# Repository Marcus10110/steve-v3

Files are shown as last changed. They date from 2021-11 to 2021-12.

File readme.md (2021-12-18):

# Steve the Bartending Robot

PCB Revision 3

Steve the bartending robot is a robotic drink maker, capable of dispensing 24 different liquids for mixing cocktails.

## Hardware Guide

### Electronics
The Steve V3 PCB design files can be found in the BarBot3 directory.

The schematics and layout were created with [KiCad](https://www.kicad.org/)

The board can also be ordered directly from [OSHPARK](https://oshpark.com/) [here](https://oshpark.com/shared_projects/AuEMTmuf).

The bill of materials for the PCB, pumps, and wire harness for the pumps is available on [octopart](https://octopart.com/) [here](https://octopart.com/bom-tool/abOfMIaY).

The design also requires a 12V, 4A+ power supply with a 5.5x2.1mm barrel jack, and a USB-C cable, for USB 2.0 data.

The power supply current rating is the limiting factor for the number of pumps which can be turned on simultaneously.

The parts list include includes wire, connectors, and crimps for assembling the pump motor wire harnesses.

Additionally, a crimp tool is needed to crimp the connectors into the wire. **TODO: find PN and place here.**

We assembled the pumps all with the same wire length, long enough to reach from the PCB to the furthest pump with some spare distance.

The connector pin 1 should be connected to the positive side of the pump, and pin 2 should be connected to the negative side.

**TODO: add wire assembly detail here**

### Mechanical

To hold all the pumps and the PCB together. This was laser cut from acrylic. The CAD design can be found on [onshape](https://www.onshape.com/en/) [here](https://cad.onshape.com/documents/0a76c84c79ce9e6492f21b7e/w/e3ece1aa1a5ce6af157ea8d7/e/032fdd28f397ef2ffe8feb1f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).

In addition to the laser cut mount, the following parts are needed:
- [Wood Furniture Legs](https://www.amazon.com/gp/product/B07DF68BN7/ref=ppx_yo_dt_b_search_asin_image?ie=UTF8&psc=1)
- M2.5 thermal threaded inserts x48
- M3 thermal threaded inserts x3
- 3/4 inch wood screws #8 x4
- M2.5 screws x48
- M3 standoffs x3
- M3 screws x3

**TODO: add McMaster links**

### Firmware

The firmware is developed using the Arduino software, and can be found in the BarBot3Firmware folder.

The hardware implementation was based off of Sparkfun's [SparkFun Qwiic Pro Micro](https://www.sparkfun.com/products/15795), which is essentially a Sparkfun Pro Micro but with a USB-C connector.

In the arduino software, you will want to install the Sparkfun board library, and select the Sparkfun Pro Micro 3.3V / 8 MHz board. Install instructions can be found [here](https://github.com/sparkfun/Arduino_Boards#installation-instructions).

Also, install the "Adafruit MCP23008 Library" from the library manager.

It's important to mention that the microcontroller does not support USB bus power, so the 12V power supply must be connected in order for the microcontroller to run.

Before the firmware can be loaded onto the microcontroller, the Arduino bootloader needs to be loaded onto the ATMEGA32U4. This can be done in a number of ways, however the simplest is to use the AVR-ISP MK2.

**TODO: link to an actually good FW flashing article**

Once the Arduino bootloader has been flashed, the device should enumerate as a serial port over USB.

The BarBot3Firmware project should compile successfully once the required library is installed. Be sure the board mentioned above is selected. Then download the firmware.

To verify the design is working, open the serial monitor in the Arduino software, and type and send "DEBUG". This will print out a list of 24 zeros, indicating that all pumps are off. This command is for debugging only, and prints out the number of milliseconds each pump will remain on. Once a pump reaches zero, the pump will turn off.

Refer to the comments at the top of BarBat3Firmware.ino for documentation on the supported commands

**TODO: move firmware command documentation here**

### Software

**TODO: Link to SW repository here.**

## Operating Guide

**TODO: write operating guide here**

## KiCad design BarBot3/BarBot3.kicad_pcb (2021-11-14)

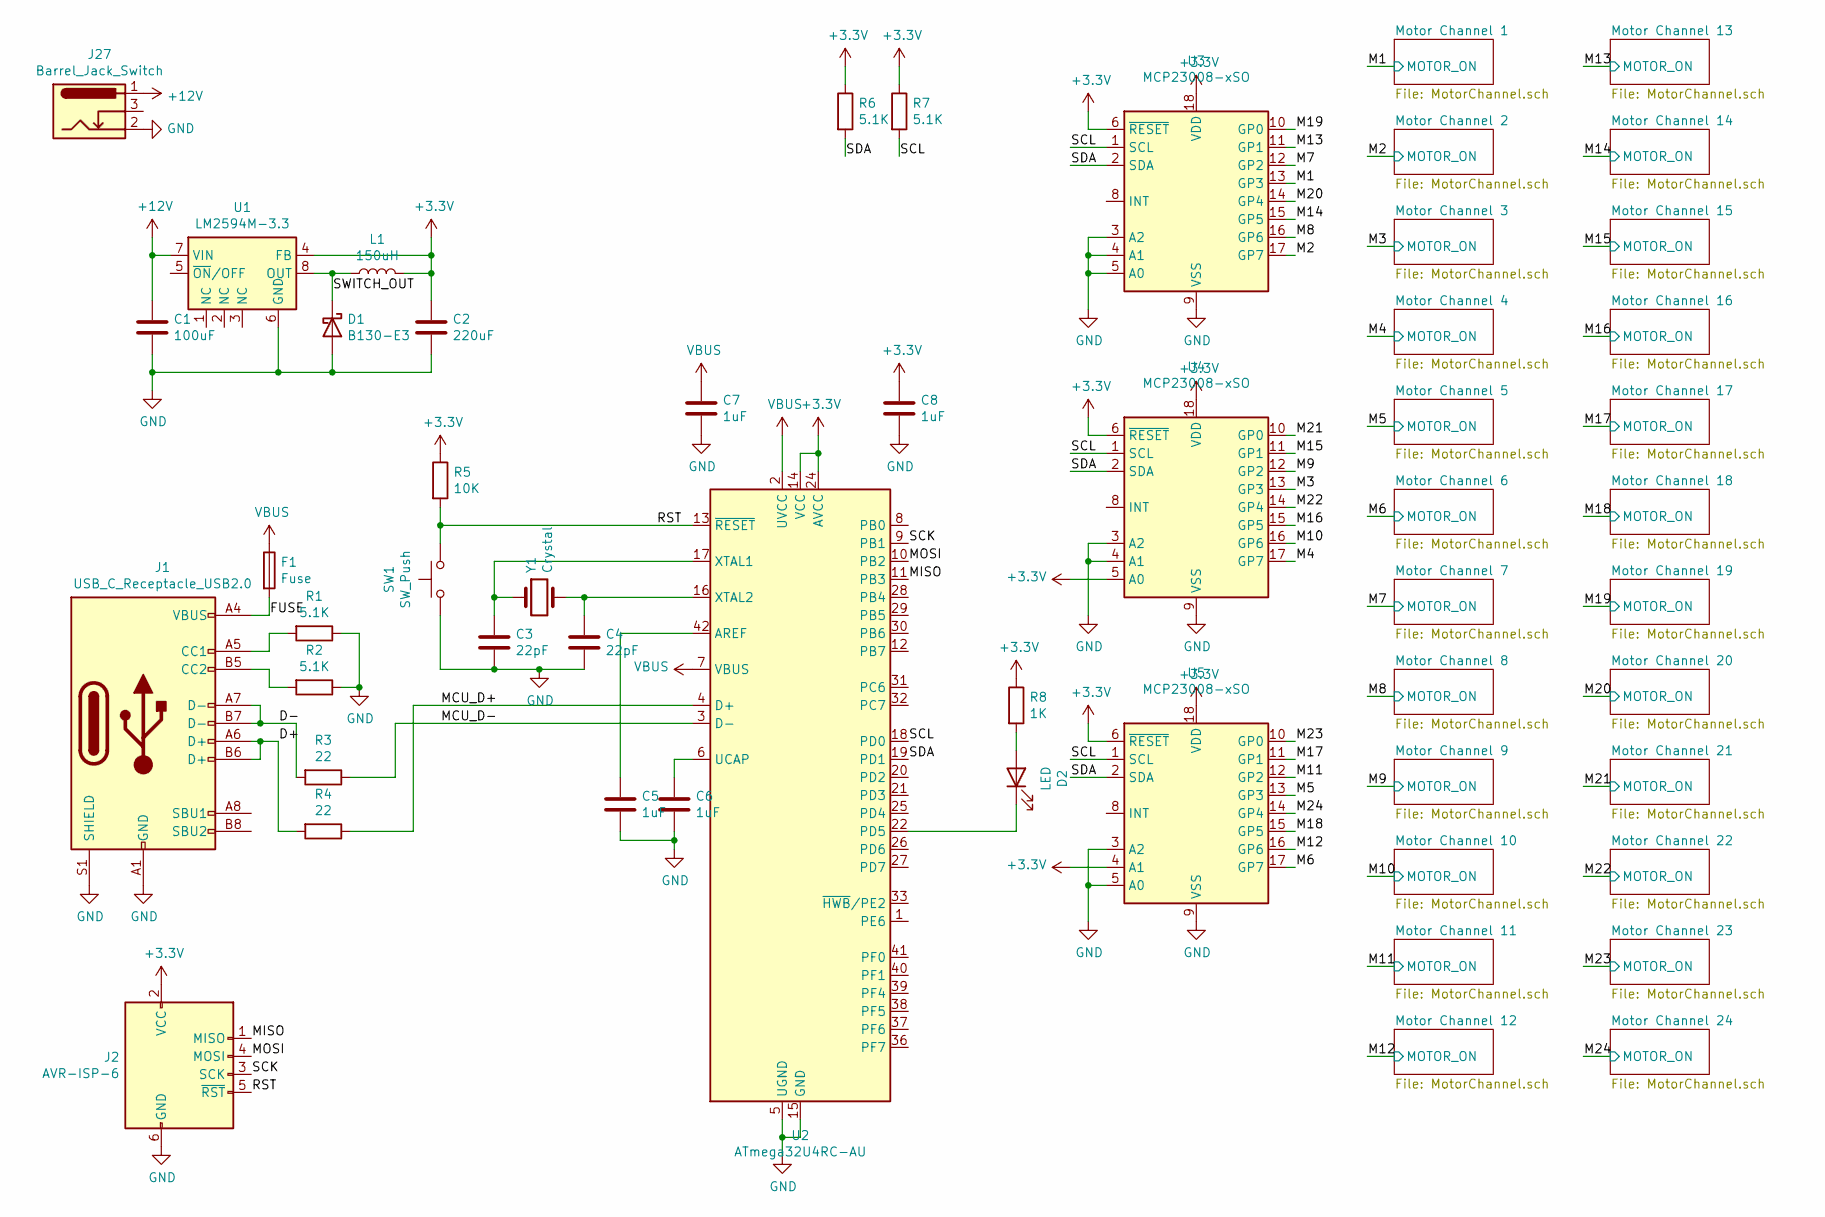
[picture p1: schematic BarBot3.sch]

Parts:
C1: 100uF; C_Elec_8x10.2
C2: 220uF; CP_Elec_10x10
C3, C4: 22pF; C_0805_2012Metric_Pad1.18x1.45mm_HandSolder
C5, C6, C7, C8: 1uF; C_0805_2012Metric_Pad1.18x1.45mm_HandSolder
D1: B130-E3; D_SOD-123
D2: LED; LED_PLCC-2
F1: Fuse; Fuse_1206_3216Metric_Pad1.42x1.75mm_HandSolder
J1: USB_C_Receptacle_USB2.0; USB_C_Receptacle_GCT_USB4085
J2: AVR-ISP-6; PinHeader_2x03_P2.54mm_Vertical
J27: Barrel_Jack_Switch; BarrelJack_CUI_PJ-102AH_Horizontal
L1: 150uH; L_Bourns_SRR1210A
R1, R2, R6, R7: 5.1K; R_0805_2012Metric_Pad1.20x1.40mm_HandSolder
R3, R4: 22; R_0805_2012Metric_Pad1.20x1.40mm_HandSolder
R5: 10K; R_0805_2012Metric_Pad1.20x1.40mm_HandSolder
R8: 1K; R_0805_2012Metric_Pad1.20x1.40mm_HandSolder
SW1: SW_Push; SW_Push_1P1T_NO_6x6mm_H9.5mm
U1: LM2594M-3.3; SOIC-8_3.9x4.9mm_P1.27mm
U2: ATmega32U4RC-AU; TQFP-44_10x10mm_P0.8mm
U3, U4, U5: MCP23008-xSO; SOIC-18W_7.5x11.6mm_P1.27mm
Y1: Crystal; Crystal_SMD_HC49-SD_HandSoldering

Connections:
+3V3: C2.1, C8.1, J2.2 (VCC), L1.2, R5.1, R6.1, R7.1, R8.1, U1.4 (FB), U2.14 (VCC), U2.24 (AVCC), U2.34 (VCC), U2.44 (AVCC), U3.6 (~RESET), U3.18 (VDD), U4.5 (A0), U4.6 (~RESET), U4.18 (VDD), U5.4 (A1), U5.6 (~RESET), U5.18 (VDD)
+12V: C1.1, J27.1, U1.7 (VIN); also elsewhere on the board
/D+: J1.A6 (D+), J1.B6 (D+), R4.2
/D-: J1.A7 (D-), J1.B7 (D-), R3.2
/FUSE: F1.2, J1.A4 (VBUS), J1.A9 (VBUS), J1.B4 (VBUS), J1.B9 (VBUS)
/M1: U3.13 (GP3); also elsewhere on the board
/M2: U3.17 (GP7); also elsewhere on the board
/M3: U4.13 (GP3); also elsewhere on the board
/M4: U4.17 (GP7); also elsewhere on the board
/M5: U5.13 (GP3); also elsewhere on the board
/M6: U5.17 (GP7); also elsewhere on the board
/M7: U3.12 (GP2); also elsewhere on the board
/M8: U3.16 (GP6); also elsewhere on the board
/M9: U4.12 (GP2); also elsewhere on the board
/M10: U4.16 (GP6); also elsewhere on the board
/M11: U5.12 (GP2); also elsewhere on the board
/M12: U5.16 (GP6); also elsewhere on the board
/M13: U3.11 (GP1); also elsewhere on the board
/M14: U3.15 (GP5); also elsewhere on the board
/M15: U4.11 (GP1); also elsewhere on the board
/M16: U4.15 (GP5); also elsewhere on the board
/M17: U5.11 (GP1); also elsewhere on the board
/M18: U5.15 (GP5); also elsewhere on the board
/M19: U3.10 (GP0); also elsewhere on the board
/M20: U3.14 (GP4); also elsewhere on the board
/M21: U4.10 (GP0); also elsewhere on the board
/M22: U4.14 (GP4); also elsewhere on the board
/M23: U5.10 (GP0); also elsewhere on the board
/M24: U5.14 (GP4); also elsewhere on the board
/MCU_D+: R4.1, U2.4 (D+)
/MCU_D-: R3.1, U2.3 (D-)
/MISO: J2.1 (MISO), U2.11 (PB3)
/MOSI: J2.4 (MOSI), U2.10 (PB2)
/RST: J2.5 (~RST), R5.2, SW1.2, U2.13 (~RESET)
/SCK: J2.3 (SCK), U2.9 (PB1)
/SCL: R7.2, U2.18 (PD0), U3.1 (SCL), U4.1 (SCL), U5.1 (SCL)
/SDA: R6.2, U2.19 (PD1), U3.2 (SDA), U4.2 (SDA), U5.2 (SDA)
/SWITCH_OUT: D1.1 (K), L1.1, U1.8 (OUT)
GND: C1.2, C2.2, C3.2, C4.2, C5.2, C6.2, C7.2, C8.2, D1.2 (A), J1.A1 (GND), J1.A12 (GND), J1.B1 (GND), J1.B12 (GND), J1.S1 (SHIELD), J2.6 (GND), J27.2, R1.1, R2.1, SW1.1, U1.6 (GND), U2.5 (UGND), U2.15 (GND), U2.23 (GND), U2.35 (GND), U2.43 (GND), U3.3 (A2), U3.4 (A1), U3.5 (A0), U3.9 (VSS), U4.3 (A2), U4.4 (A1), U4.9 (VSS), U5.3 (A2), U5.5 (A0), U5.9 (VSS); also elsewhere on the board
unnamed: C3.1, U2.17 (XTAL1), Y1.1
unnamed: C4.1, U2.16 (XTAL2), Y1.2
unnamed: C5.1, U2.42 (AREF)
unnamed: C6.1, U2.6 (UCAP)
unnamed: D2.1 (K), U2.22 (PD5)
unnamed: D2.2 (A), R8.2
unnamed: J1.A5 (CC1), R1.2
unnamed: J1.B5 (CC2), R2.2
VBUS: C7.1, F1.1, U2.2 (UVCC), U2.7 (VBUS)

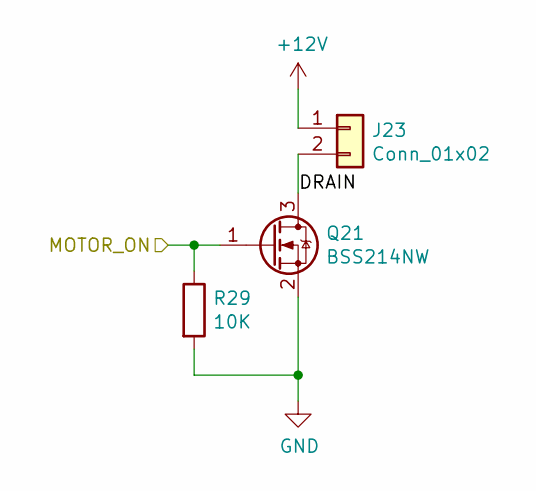
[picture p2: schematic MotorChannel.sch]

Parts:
J3: Conn_01x02; Hirose_DF3EA-02P-2V_1x02-1MP_P2.00mm_Vertical
Q1: BSS214NW; SOT-323_SC-70
R9: 10K; R_0805_2012Metric_Pad1.20x1.40mm_HandSolder

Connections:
+12V: J3.1; also elsewhere on the board
/M1: Q1.1 (G), R9.1; also elsewhere on the board
/Motor Channel 1/DRAIN: J3.2, Q1.3 (D)
GND: Q1.2 (S), R9.2; also elsewhere on the board

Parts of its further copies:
J4, J5, J6, J7, J8, J9, J10, J11, J12, J13, J14, J15, J16, J17, J18, J19, J20, J21, J22, J23, J24, J25, J26: Conn_01x02; Hirose_DF3EA-02P-2V_1x02-1MP_P2.00mm_Vertical
Q2, Q3, Q4, Q5, Q6, Q7, Q8, Q9, Q10, Q11, Q12, Q13, Q14, Q15, Q16, Q17, Q18, Q19, Q20, Q21, Q22, Q23, Q24: BSS214NW; SOT-323_SC-70
R10, R11, R12, R13, R14, R15, R16, R17, R18, R19, R20, R21, R22, R23, R24, R25, R26, R27, R28, R29, R30, R31, R32: 10K; R_0805_2012Metric_Pad1.20x1.40mm_HandSolder

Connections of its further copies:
+12V: J4.1, J5.1, J6.1, J7.1, J8.1, J9.1, J10.1, J11.1, J12.1, J13.1, J14.1, J15.1, J16.1, J17.1, J18.1, J19.1, J20.1, J21.1, J22.1, J23.1, J24.1, J25.1, J26.1; also elsewhere on the board
/M2: Q2.1 (G), R10.1; also elsewhere on the board
/M3: Q3.1 (G), R11.1; also elsewhere on the board
/M4: Q4.1 (G), R12.1; also elsewhere on the board
/M5: Q5.1 (G), R13.1; also elsewhere on the board
/M6: Q6.1 (G), R14.1; also elsewhere on the board
/M7: Q7.1 (G), R15.1; also elsewhere on the board
/M8: Q8.1 (G), R16.1; also elsewhere on the board
/M9: Q9.1 (G), R17.1; also elsewhere on the board
/M10: Q10.1 (G), R18.1; also elsewhere on the board
/M11: Q11.1 (G), R19.1; also elsewhere on the board
/M12: Q12.1 (G), R20.1; also elsewhere on the board
/M13: Q13.1 (G), R21.1; also elsewhere on the board
/M14: Q14.1 (G), R22.1; also elsewhere on the board
/M15: Q15.1 (G), R23.1; also elsewhere on the board
/M16: Q16.1 (G), R24.1; also elsewhere on the board
/M17: Q17.1 (G), R25.1; also elsewhere on the board
/M18: Q18.1 (G), R26.1; also elsewhere on the board
/M19: Q19.1 (G), R27.1; also elsewhere on the board
/M20: Q20.1 (G), R28.1; also elsewhere on the board
/M21: Q21.1 (G), R29.1; also elsewhere on the board
/M22: Q22.1 (G), R30.1; also elsewhere on the board
/M23: Q23.1 (G), R31.1; also elsewhere on the board
/M24: Q24.1 (G), R32.1; also elsewhere on the board
/Motor Channel 2/DRAIN: J4.2, Q2.3 (D)
/Motor Channel 3/DRAIN: J5.2, Q3.3 (D)
/Motor Channel 4/DRAIN: J6.2, Q4.3 (D)
/Motor Channel 5/DRAIN: J7.2, Q5.3 (D)
/Motor Channel 6/DRAIN: J8.2, Q6.3 (D)
/Motor Channel 7/DRAIN: J9.2, Q7.3 (D)
/Motor Channel 8/DRAIN: J10.2, Q8.3 (D)
/Motor Channel 9/DRAIN: J11.2, Q9.3 (D)
/Motor Channel 10/DRAIN: J12.2, Q10.3 (D)
/Motor Channel 11/DRAIN: J13.2, Q11.3 (D)
/Motor Channel 12/DRAIN: J14.2, Q12.3 (D)
/Motor Channel 13/DRAIN: J15.2, Q13.3 (D)
/Motor Channel 14/DRAIN: J16.2, Q14.3 (D)
/Motor Channel 15/DRAIN: J17.2, Q15.3 (D)
/Motor Channel 16/DRAIN: J18.2, Q16.3 (D)
/Motor Channel 17/DRAIN: J19.2, Q17.3 (D)
/Motor Channel 18/DRAIN: J20.2, Q18.3 (D)
/Motor Channel 19/DRAIN: J21.2, Q19.3 (D)
/Motor Channel 20/DRAIN: J22.2, Q20.3 (D)
/Motor Channel 21/DRAIN: J23.2, Q21.3 (D)
/Motor Channel 22/DRAIN: J24.2, Q22.3 (D)
/Motor Channel 23/DRAIN: J25.2, Q23.3 (D)
/Motor Channel 24/DRAIN: J26.2, Q24.3 (D)
GND: Q2.2 (S), Q3.2 (S), Q4.2 (S), Q5.2 (S), Q6.2 (S), Q7.2 (S), Q8.2 (S), Q9.2 (S), Q10.2 (S), Q11.2 (S), Q12.2 (S), Q13.2 (S), Q14.2 (S), Q15.2 (S), Q16.2 (S), Q17.2 (S), Q18.2 (S), Q19.2 (S), Q20.2 (S), Q21.2 (S), Q22.2 (S), Q23.2 (S), Q24.2 (S), R10.2, R11.2, R12.2, R13.2, R14.2, R15.2, R16.2, R17.2, R18.2, R19.2, R20.2, R21.2, R22.2, R23.2, R24.2, R25.2, R26.2, R27.2, R28.2, R29.2, R30.2, R31.2, R32.2; also elsewhere on the board

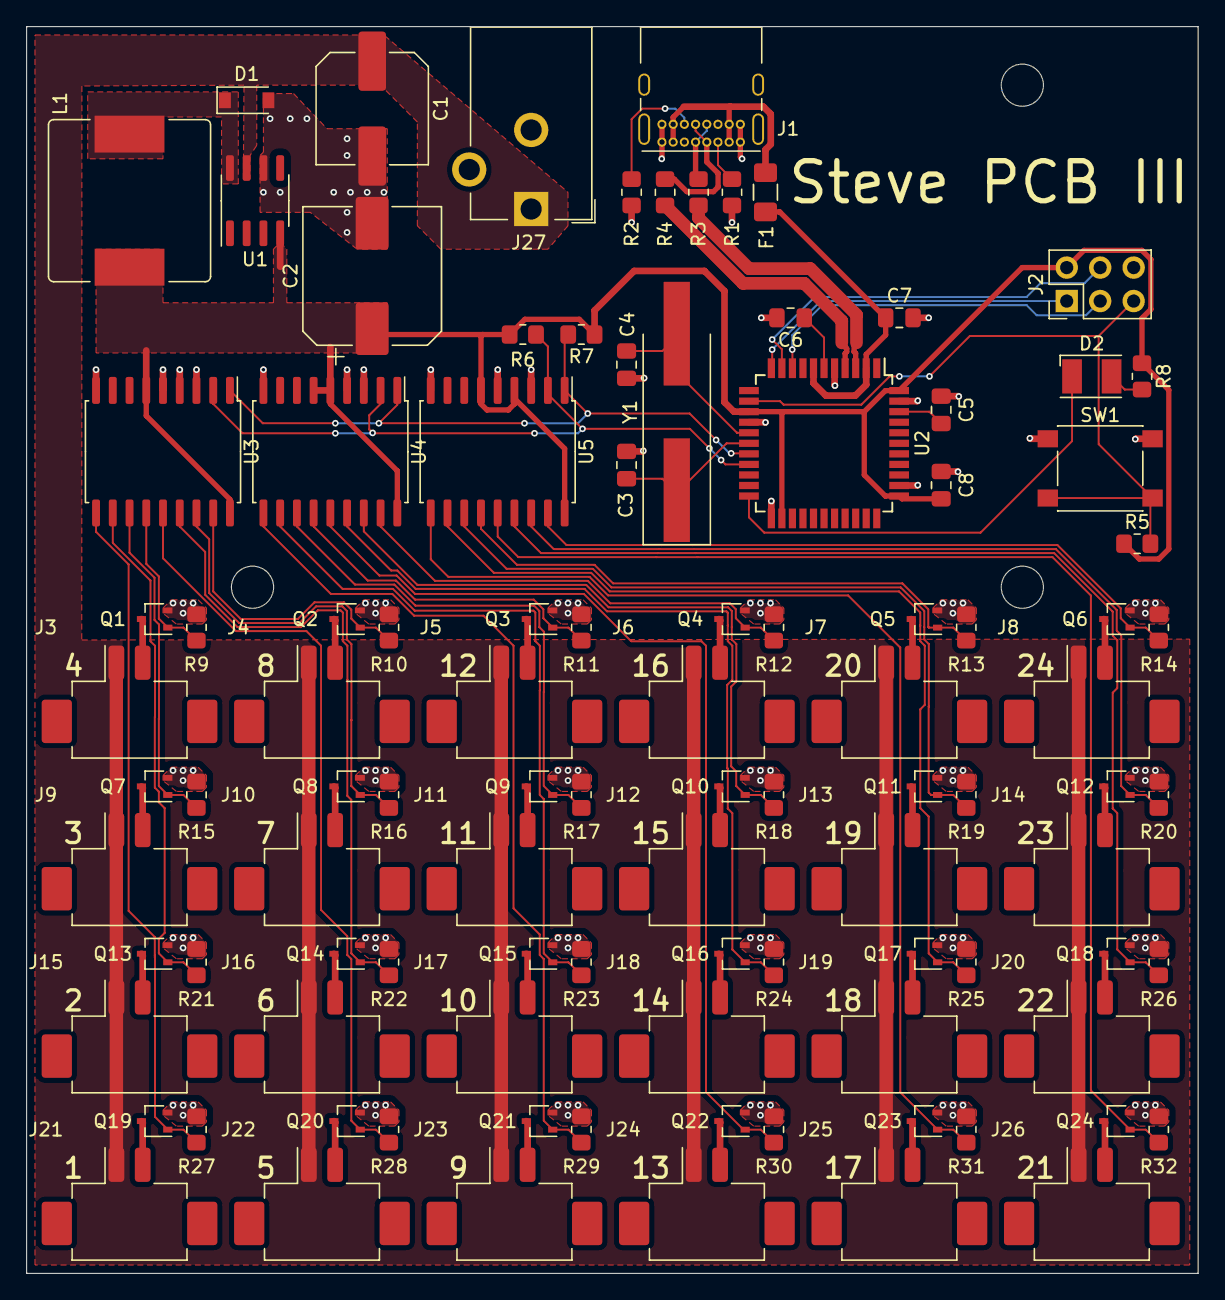
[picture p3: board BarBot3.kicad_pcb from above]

Board: 2 copper layers, 88.9 x 94.6 mm, 102 parts (0 on the bottom side), 72 nets.

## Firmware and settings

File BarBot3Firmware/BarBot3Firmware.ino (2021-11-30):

#include <Adafruit_MCP23008.h>

// Pin mapping diagram for the 32u4: https://www.arduino.cc/en/Hacking/PinMapping32u4
// Adafruit port expander library: https://github.com/adafruit/Adafruit-MCP23008-library

// Commands:
// start pumps
// takes the time, in seconds, each of the 24 pumps should run.
// must have exactly 24 values, and follow the format below.
// no return value.
// PUMP,0,1,2,3,4,5,6,7,8,9,10,11,12,13,14,15,16,17,18,19,20,21,22,23\n

// STATUS\n
// prints the number of seconds remaining for the current drink, followed by a \n.

// DEBUG\n
// prints the number of miliseconds remaining for each pump
// example result: status: 0 0 0 0 0 0 0 0 0 0 0 834 1834 2834 3834 4834 5834 6834 7834 8834 9834 10834 11834 12834

#define LED_PIN LED_BUILTIN_TX // PD5, pin 22

Adafruit_MCP23008 PortExpanders[3];

struct MotorAddress
{
  uint8_t mIoPin;
  uint8_t mI2CAddress;
};

MotorAddress MotorPins[] = {
    {3, 0},
    {7, 0},
    {3, 1},
    {7, 1},
    {3, 2},
    {7, 2},
    {2, 0},
    {6, 0},
    {2, 1},
    {6, 1},
    {2, 2},
    {6, 2},
    {1, 0},
    {5, 0},
    {1, 1},
    {5, 1},
    {1, 2},
    {5, 2},
    {0, 0},
    {4, 0},
    {0, 1},
    {4, 1},
    {0, 2},
    {4, 2}};

constexpr int PumpCount = 24;

int ParsePumpIndex = 0;
bool ParsingValues = false;
uint32_t PumpTimeRemainingMs[PumpCount] = {0};
int ParsedPumpValues[PumpCount] = {0};
String Buffer;
uint32_t LastServicedTimeMs = 0;

void setup()
{
  LastServicedTimeMs = millis();
  Serial.begin(9600);
  while (!Serial)
  {
  };
  Serial.println("Steve III");

  pinMode(LED_PIN, OUTPUT);
  digitalWrite(LED_PIN, HIGH);
  assert(PortExpanders[0].begin(0));
  assert(PortExpanders[1].begin(1));
  assert(PortExpanders[2].begin(2));

  for (auto &port_expander : PortExpanders)
  {
    for (int i = 0; i < 8; ++i)
    {
      assert(port_expander.digitalWrite(i, LOW));
      assert(port_expander.pinMode(i, OUTPUT));
    }
  }
}

void loop()
{
  while (Serial.available() > 0)
  {
    bool complete_command = Parse(Serial.read());
    if (complete_command)
    {
      HandleNewPumpValues();
      break;
    }
  }
  ServicePumps();
}

void HandleNewPumpValues()
{
  for (int i = 0; i < PumpCount; ++i)
  {
    PumpTimeRemainingMs[i] = ParsedPumpValues[i] * 1000ul;
    LastServicedTimeMs = millis();
  }
}

void ServicePumps()
{
  auto now = millis();
  if (now < LastServicedTimeMs)
  {
    LastServicedTimeMs = now;
    return;
  }
  auto elapsed = now - LastServicedTimeMs;
  LastServicedTimeMs = now;
  bool any_on = false;
  for (int i = 0; i < PumpCount; ++i)
  {
    auto delta = min(PumpTimeRemainingMs[i], elapsed);
    PumpTimeRemainingMs[i] -= delta;
    bool on = PumpTimeRemainingMs[i] > 0;
    any_on |= on;
    SetMotor(i, on);
  }
  digitalWrite(LED_PIN, !any_on);
}

void SetMotor(int motor, bool on)
{
  assert(motor <= 23);
  const auto &pin = MotorPins[motor];
  PortExpanders[pin.mI2CAddress].digitalWrite(pin.mIoPin, on);
}

// never returns
void assert(bool check)
{
  if (check)
    return;
  Serial.println("Assert check failed.");
  while (true)
  {
    digitalWrite(LED_PIN, true);
    delay(100);
    digitalWrite(LED_PIN, false);
    delay(100);
  }
}

// parses one character at a time. returns true when all 24 pumps have been updated.
bool Parse(char x)
{
  if (x == ',')
  {
    ParseBuffer(Buffer);
    Buffer = "";
  }
  else if (x == '\n')
  {
    ParseBuffer(Buffer);
    Buffer = "";
    bool done = ParsingValues && ParsePumpIndex == 24;
    ParsePumpIndex = 0;
    ParsingValues = false;
    return done;
  }
  else
  {
    Buffer += x;
  }
  return false;
}

void ParseBuffer(const String &buffer)
{
  if (buffer == "PUMP")
  {
    ParsePumpIndex = 0;
    ParsingValues = true;
  }
  else if (buffer == "STATUS")
  {
    ParsePumpIndex = 0;
    ParsingValues = false;
    SendStatus();
  }
  else if (buffer == "DEBUG")
  {
    SendDebug();
  }
  else if (ParsingValues && ParsePumpIndex < PumpCount)
  {
    ParsedPumpValues[ParsePumpIndex++] = buffer.toInt();
  }
}

void SendDebug()
{
  Serial.print("status: ");
  for (auto pump : PumpTimeRemainingMs)
  {
    Serial.print(pump);
    Serial.print(" ");
  }
  Serial.println("");
}

void SendStatus()
{
  uint32_t longest_time = 0;
  for (auto pump : PumpTimeRemainingMs)
  {
    if (pump > longest_time)
    {
      longest_time = pump;
    }
  }
  Serial.println(longest_time / 1000);
}

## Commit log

2021-11-14 First commit. This version was submitted for fabrication
    [BarBot3.kicad_pcb, BarBot3.sch, MotorChannel.sch]
2021-11-30 added arduino firmware
